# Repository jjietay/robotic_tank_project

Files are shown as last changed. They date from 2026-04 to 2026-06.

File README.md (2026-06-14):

# Autonomous Robotic Tank

<p align="center">
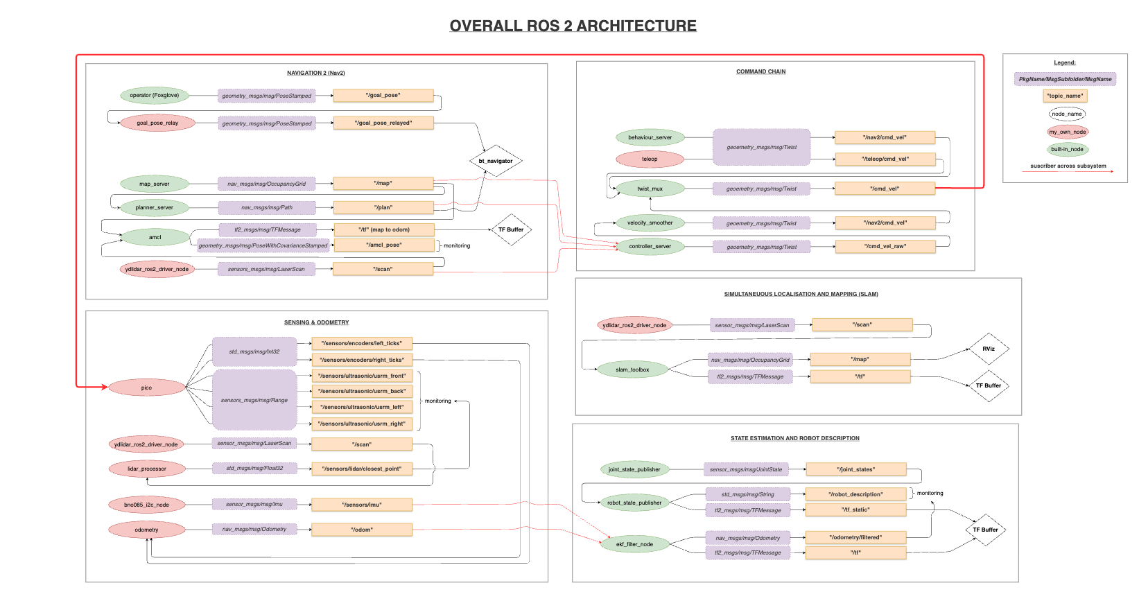
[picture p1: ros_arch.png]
Overall ROS 2 architecture
  
</p>

<p align="center">
  <a href="https://jjietay.github.io/robotic_tank_project/index.html">
    <strong>Read my full documentation & project journey!</strong>
  </a>
</p>

Hi there! Here's a look into my Autonomous Robotic Tank Project. Visit my website in the link above to see my reflection at every stage of this project.

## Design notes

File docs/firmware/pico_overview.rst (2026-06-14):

Pico Overview
=============

See also: :doc:`main.cpp <main_cpp>`

Purpose
-------

Pico W takes care of the hardware.

The Pico W is responsible for:

- Driving the motors through the Cytron motor driver
- Reading the wheel encoders using GPIO interrupts
- Measuring distance with the ultrasonic sensors
- Talking to the ROS 2 system on the Raspberry Pi over micro ROS

Topics
------

The firmware uses these ROS topics:

- ``/cmd_vel`` for the incoming motion command
- ``/sensors/ultrasonic/usrm_front``
- ``/sensors/ultrasonic/usrm_back``
- ``/sensors/ultrasonic/usrm_left``
- ``/sensors/ultrasonic/usrm_right``
- ``/sensors/encoders/left_ticks``
- ``/sensors/encoders/right_ticks``

Layout
------

All of the firmware are in one ``main.cpp`` file + a small set of classes,
motors, encoders, ultrasonic sensors, and PID controller. Shared settings such as pins, robot size, and gains are in ``config.hpp``.

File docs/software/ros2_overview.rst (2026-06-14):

ROS 2 Overview
==============

This page gives a short overview of the ROS 2 software that runs on the
Raspberry Pi 4. The Raspberry Pi handles sensing, state estimation, mapping,
navigation, and the commands that drive the tank. The Pico W handles the low
level motor and sensor work and talks to the Pi over a serial micro ROS link.

The system is made up of a few groups of nodes.

Sensing
    The Pico W publishes wheel encoder ticks and ultrasonic ranges. The lidar
    driver publishes laser scans on ``/scan``. The BNO085 IMU node publishes
    orientation and motion on ``/sensors/imu``.

State estimation
    The odometry node turns encoder ticks into a pose estimate on ``/odom``.
    The EKF from robot_localization fuses ``/odom`` and ``/sensors/imu`` into a
    smoother estimate and broadcasts the ``odom`` to ``base_link`` transform.

Mapping and navigation
    SLAM Toolbox builds a map from the laser scans. Nav2 plans a path to a goal
    and follows it, sending velocity commands for the tank to follow.

Commands
    More than one source can ask the tank to move. Teleop sends keyboard
    commands and Nav2 sends its own commands. The twist_mux node picks one
    based on priority and forwards it as ``/cmd_vel``, which the Pico W reads.

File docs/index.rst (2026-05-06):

Documentation
========================

This documentation covers the full robotic tank project:
My learning process, ROS 2 software on the Raspberry Pi, firmware on the Pico W,
and hardware design and calibration.

.. toctree::
    :maxdepth: 2
    :caption: Sections:

    learning/index
    software/index
    firmware/index

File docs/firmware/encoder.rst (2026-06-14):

Encoder
=======

See also: :doc:`main.cpp <main_cpp>`

Purpose
-------

The ``Encoder`` class reads how far each wheel has turned. It counts the pulses
from a quadrature encoder using GPIO interrupts, and it can report both the tick
count and the wheel speed in metres per second.

How quadrature works
--------------------

A quadrature encoder gives two square wave signals, channel A and channel B,
that are a quarter cycle apart. As the shaft turns, each channel produces rising
and falling edges. The order of the edges on A and B tells you which way the
wheel is turning.

.. list-table::
    :header-rows: 1
    :widths: 30 30 40

    *   - Event
        - Condition
        - Result
    *   - Pin A rises
        - B is LOW (A is not equal to B)
        - ``count++`` (forward)
    *   - Pin A rises
        - B is HIGH (A equals B)
        - ``count--`` (backward)
    *   - Pin B rises
        - A is HIGH (A equals B)
        - ``count++`` (forward)
    *   - Pin B rises
        - A is LOW (A is not equal to B)
        - ``count--`` (backward)

The ``count`` variable is marked ``volatile`` because it is changed inside the
interrupt handler and read in the main loop. That tells the compiler to always
read it back from memory instead of keeping a stale copy in a register.

Scenario 1: A leads B (forward)
-------------------------------

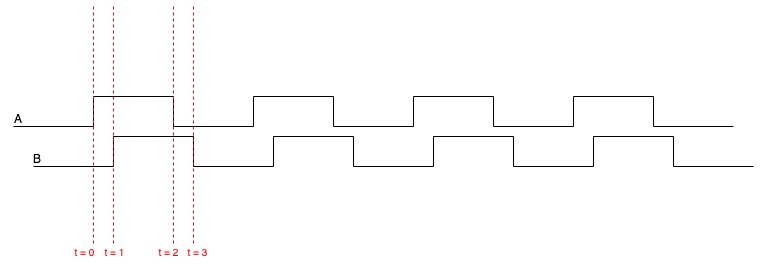
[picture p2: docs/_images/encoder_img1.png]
A leading B


- At t=0, A rises while B is still LOW, so ``count++``
- At t=1, B rises while A is HIGH, so ``count++``
- The result is two counts forward

Scenario 2: B leads A (backward)
--------------------------------

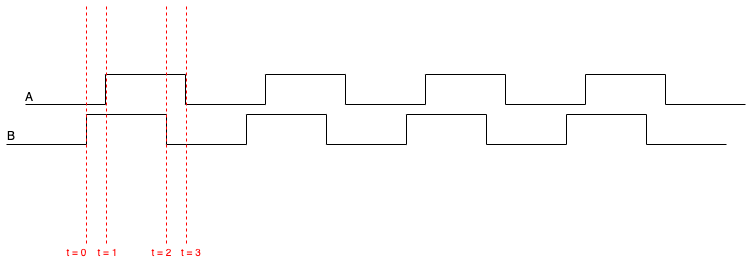
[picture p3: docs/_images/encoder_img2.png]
B leading A


- At t=0, B rises while A is still LOW, so ``count--``
- At t=1, A rises while B is HIGH, so ``count--``
- The result is two counts backward

.. note::

    The count tracks net movement, not total distance. If the tank rolls
    forward one metre and then back one metre, the count returns to zero.

Counts per wheel turn
---------------------

The number of counts for one full turn of the wheel depends on the encoder
pulses, the gearbox, and the fact that the decoder counts both edges of both
channels:

.. math::

    \text{counts per wheel turn} = 4 \times \text{PPR} \times \text{gear reduction}

For this tank the encoder has 11 pulses per motor turn and the gearbox reduction
is 131, so:

.. math::

    4 \times 11 \times 131 = 5764 \text{ counts per wheel turn}

Setup
-----

The constructor works out the wheel circumference from the diameter, works out
the counts per wheel turn, and sets up the pins. Both channel pins are inputs
with pull up resistors, which hold them HIGH when there is no signal and stop
false edges from electrical noise.

The Pico allows only one GPIO interrupt callback per core. So the first encoder
registers the shared callback, and any later encoder only enables its pins and
reuses that same callback:

.. code-block:: cpp

    gpio_set_irq_enabled_with_callback(pin_a, GPIO_IRQ_EDGE_RISE | GPIO_IRQ_EDGE_FALL,
                                       true, &Encoder::irq_handler);

    gpio_set_irq_enabled(pin_a, GPIO_IRQ_EDGE_RISE | GPIO_IRQ_EDGE_FALL, true);
    gpio_set_irq_enabled(pin_b, GPIO_IRQ_EDGE_RISE | GPIO_IRQ_EDGE_FALL, true);

Handling the interrupt
----------------------

Every edge goes to the one static ``irq_handler``, which loops over the
registered encoders and calls ``handle_irq`` on each. ``handle_irq`` first
checks that the pin belongs to that encoder, then applies the quadrature rule
to move the count up or down.

Methods
-------

.. cpp:function:: int get_count()

Returns the signed tick count. Interrupts are turned off for the moment of the
read so the value cannot change halfway through. If the encoder was set up as
inverted, the sign is flipped.

.. cpp:function:: float get_vel()

Returns the wheel speed in metres per second. It works out the time since the
last call, finds the change in counts, turns that into a distance, and divides
by the time:

.. math::

    v = \frac{\Delta\text{counts}}{\text{counts per wheel turn}} \times
        \frac{C}{\Delta t}

where ``C`` is the wheel circumference. The time step is floored at one
millisecond to keep the result steady, the first call returns zero, and the
speed is passed through an exponential moving average so it is smoother.

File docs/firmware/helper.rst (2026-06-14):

Helper Functions
================

See also: :doc:`main.cpp <main_cpp>`

Purpose
-------

These are the small helper functions in ``main.cpp``.

clampf
------

.. code-block:: cpp

   static inline float clampf(float x, float lo, float hi)
   {
       if (x < lo) return lo;
       if (x > hi) return hi;
       return x;
   }

Keeps a value inside a low and high limit. The control loop uses it to keep the
motor duty inside the range from -1 to 1 after the feedforward and
PID are added together.

init_range_msg
--------------

.. code-block:: cpp

   static void init_range_msg(sensor_msgs__msg__Range* msg, uint8_t rad_type,
                              float fov, float min_r, float max_r)
   {
       msg->radiation_type = rad_type;
       msg->field_of_view  = fov;
       msg->min_range = min_r;
       msg->max_range = max_r;
       msg->range  = 0.0f;
   }

Fills in the fixed fields of a range message: the type, the cone angle, and the
smallest and largest distance the sensor can report. The four ultrasonic
messages are set up with the same call, so they all share the same settings and
only differ in their frame name and their measured value.

set_msg_stamp
-------------

.. code-block:: cpp

   static void set_msg_stamp(std_msgs__msg__Header* header)
   {
       uint64_t now_us = time_us_64();
       header->stamp.sec = now_us / 1000000ULL;
       header->stamp.nanosec = (now_us % 1000000ULL) * 1000ULL;
   }

Stamps a message with the current time from the Pico clock, split into seconds
and nanoseconds the way ROS 2 expects. Every published message uses this same
clock, which keeps the timestamps consistent for the Raspberry Pi to use.

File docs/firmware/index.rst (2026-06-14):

Firmware
========

This section covers the firmware that runs on the Pico W. The Pico W drives the motors, reads the wheel
encoders, fires the ultrasonic sensors, and communicates to the Raspberry Pi over a
serial micro ROS link.

Overview
--------

.. toctree::
    :maxdepth: 2

    pico_overview

Code
----

.. toctree::
    :maxdepth: 2

    main_cpp

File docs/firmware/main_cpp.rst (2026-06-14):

main.cpp
========

See also: :doc:`Pico Overview <pico_overview>`

Purpose
-------

``main.cpp`` sets up the hardware, sets up the
micro ROS link, and then runs the control loop that keeps the tank moving.

What it does
------------

- Sets up GPIO, PWM, timing, and interrupts
- Builds the four ultrasonic sensors, the motor driver, the two encoders, and
  the two PID controllers
- Sets up the micro ROS node, the ``/cmd_vel`` subscriber, and the publishers
- Reads ``/cmd_vel`` and turns it into a target speed for each track
- Publishes ultrasonic ranges and encoder ticks back to ROS 2
- Runs the control loop at 100 Hz

Structure
---------

The file is split into a few parts:

- The :doc:`Electronics <main_cpp>` base class gives every hardware class a name
  and a status
- :doc:`Ultrasonic <ultrasonic>` measures distance with a timeout
- :doc:`Motor <motor>` drives the Cytron motor driver
- :doc:`Encoder <encoder>` counts wheel ticks using interrupts and works out
  wheel speed
- :doc:`PID <pid>` corrects the wheel speed
- :doc:`micro ROS <microros>` holds the subscriber, the publishers, and the
  command callback
- :doc:`Helper functions <helper>` set up range messages, stamp messages, and
  clamp values
- :doc:`main() Loop <main_loop>` runs the repeating control cycle

Related components
------------------

.. toctree::
    :maxdepth: 1

    encoder
    ultrasonic
    motor
    pid
    helper
    microros
    main_loop

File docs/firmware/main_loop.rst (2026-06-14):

main() Loop
===========

See also: :doc:`main.cpp <main_cpp>`

Startup
-------

Before the loop starts, ``main()`` does a one time setup:

1. Starts USB and serial output, then waits two seconds so the host can attach.
2. Builds the four ultrasonic sensors, the motor driver, the two encoders, and
   the two PID controllers.
3. Sets up the micro ROS transport over the Pico UART and creates a node named
   ``pico``.
4. Creates the ``/cmd_vel`` subscriber and the publishers for the ultrasonic
   ranges and the encoder ticks.
5. Fills in the range message settings and the frame names.
6. Adds the ``/cmd_vel`` subscription to the executor.

The publishers and subscriber are:

.. list-table::
   :header-rows: 1
   :widths: 30 35 35

   * - Role
     - Topic
     - Message type
   * - Subscriber
     - ``/cmd_vel``
     - ``geometry_msgs/msg/Twist``
   * - Ultrasonic publishers (4x)
     - ``/sensors/ultrasonic/usrm_*``
     - ``sensor_msgs/msg/Range``
   * - Encoder publishers (2x)
     - ``/sensors/encoders/*_ticks``
     - ``std_msgs/msg/Int32``

The control loop
----------------

After setup, ``main()`` runs forever at about 100 Hz. Each pass through the
loop does the following.

1. Mark the time
~~~~~~~~~~~~~~~~

The loop records the start time so it can pace itself to 100 Hz at the end.

2. Handle ROS messages
~~~~~~~~~~~~~~~~~~~~~~~

.. code-block:: cpp

   rclc_executor_spin_some(&executor, RCL_MS_TO_NS(2));

This gives the executor a short period of time to read new micro ROS messages.
When a new ``/cmd_vel`` arrives, the callback updates the left and right target
speeds in metres per second.

3. Fire one ultrasonic sensor
~~~~~~~~~~~~~~~~~~~~~~~~~~~~~

Only one ultrasonic sensor fires per cycle, and only on every third cycle. A
rotating index picks the front, back, right, or left sensor in turn. The chosen
sensor takes a reading, the range and timestamp are filled in, and the message
is published. Spacing the sensors out keeps a slow reading from blocking the
loop timing.

4. Read the command and check the watchdog
~~~~~~~~~~~~~~~~~~~~~~~~~~~~~~~~~~~~~~~~~~~

The loop copies the latest target speeds. If no ``/cmd_vel`` has arrived for
more than 500 ms, both targets are set to zero, so the tank stops if the link
goes quiet.

5. Safety stop
~~~~~~~~~~~~~~

The loop looks at the average target speed to decide if the tank wants to go
forward or backward. If it wants to go forward and the front sensor sees an
object closer than the front stop distance, both speeds are set to zero. The
same check is done for the back sensor when reversing.

6. Feedforward and PID
~~~~~~~~~~~~~~~~~~~~~~~

The loop reads the measured speed of each wheel from the encoders. For each
side it works out a feedforward duty from the target speed, then adds the PID
correction, and clamps the result to the range from negative one to one:

.. code-block:: cpp

   float ff_l = clampf(vel_l / V_MAX_MPS, -1.0f, 1.0f);
   duty_l = clampf(ff_l + pid_l.calculate(vel_l, meas_l), -1.0f, 1.0f);

When both targets are zero, the PID controllers are reset and the duty is set
to zero, so the integral term does not build up while the tank is stopped.

7. Drive the motors
~~~~~~~~~~~~~~~~~~~

.. code-block:: cpp

   MOTOR.move(duty_l, duty_r);

The motor class takes the two duty values and sets the direction pins and PWM
levels.

8. Publish encoder ticks
~~~~~~~~~~~~~~~~~~~~~~~~

The loop reads the signed tick count from each encoder and publishes them so
the odometry node on the Raspberry Pi can use them.

9. Pace the loop
~~~~~~~~~~~~~~~~

The loop busy waits until 10 ms have passed since the start time, which gives a
steady 100 Hz rate.

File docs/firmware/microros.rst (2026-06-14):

micro ROS
=========

See also: :doc:`main.cpp <main_cpp>`

Purpose
-------

This page covers the micro ROS parts of the firmware. micro ROS is the bridge
between the ROS 2 system on the Raspberry Pi 4 and the control loop on the
Pico W.

What it sets up
---------------

The firmware creates:

- one ``/cmd_vel`` subscriber (``geometry_msgs/msg/Twist``),
- four ultrasonic range publishers (``sensor_msgs/msg/Range``),
- two encoder tick publishers (``std_msgs/msg/Int32``),
- the message buffers for each of these,
- the micro ROS support objects: the allocator, the support struct, the
  executor, and the node

Node and transport
------------------

Micro ROS uses the Pico UART as its transport, then
creates a node that shows up in the ROS 2 graph on the Raspberry Pi:

.. code-block:: cpp

   rmw_uros_set_custom_transport(
       true, NULL,
       pico_serial_transport_open,  pico_serial_transport_close,
       pico_serial_transport_write, pico_serial_transport_read);

   allocator = rcl_get_default_allocator();
   rclc_support_init(&support, 0, NULL, &allocator);
   rclc_node_init_default(&node, "pico", "", &support);

The node is named ``pico``, so tools like ``ros2 node list`` on the Pi can find
it.

The command callback
--------------------

When a ``/cmd_vel`` message arrives, the callback reads the forward speed and
the turn rate and splits them into a target speed for each track:

.. code-block:: cpp

   void cmd_vel_callback(const void* msg_in) {
       const auto* msg = (const geometry_msgs__msg__Twist*)msg_in;
       float v_mps = (float)msg->linear.x;
       float w_rps = (float)msg->angular.z;
       target_vel_l_mps = v_mps - w_rps * (WHEEL_BASE_M * 0.5f);
       target_vel_r_mps = v_mps + w_rps * (WHEEL_BASE_M * 0.5f);
       last_cmd_vel_time_us = time_us_64();
   }

This is the standard differential drive split. The forward speed moves both
tracks together, and the turn rate speeds up one track and slows the other.
Both targets are kept in metres per second, which is what the control loop and
the encoders use. The time of the last command is saved so the loop can stop
the tank if commands stop arriving.

The executor
------------

The executor checks the transport for new messages and runs the callback:

.. code-block:: cpp

   rclc_executor_init(&executor, &support.context, 1, &allocator);
   rclc_executor_add_subscription(
       &executor, &cmd_vel_sub, &cmd_vel_msg, &cmd_vel_callback, ON_NEW_DATA);

The control loop calls ``rclc_executor_spin_some`` once per cycle, so the
callback runs often without blocking the rest of the loop.

Data flow
---------

End to end, the flow is:

1. A node on the Raspberry Pi publishes ``/cmd_vel``.
2. micro ROS on the Pico reads it and updates the two target speeds.
3. The control loop reads the sensors, runs the safety checks and the PID, and
   drives the motors.
4. The ultrasonic ranges and encoder ticks are published back to ROS 2.

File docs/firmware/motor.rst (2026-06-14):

Motor
=====

See also: :doc:`main.cpp <main_cpp>`

Purpose
-------

The ``Motor`` class drives the two tracks through the Cytron MDD10A motor
driver. One ``Motor`` object controls both the left and the right side.

How it works
------------

For each side the driver has two pins:

- a direction pin that sets forward or reverse
- a PWM pin that sets the speed

In this design ``l_dir_pin`` and ``l_pwm_pin`` control the left side, and
``r_dir_pin`` and ``r_pwm_pin`` control the right side.

The move method
---------------

``move(duty_left, duty_right)`` takes a duty value for each side in the range
from negative one to one:

- ``+1`` is full speed forward,
- ``0`` is stop,
- ``-1`` is full speed reverse

Before the command reaches the pins, ``move`` does three things:

1. **Trim**

   Each side is scaled by its trim factor. This helps account for manufacturing defects for straight driving.

2. **Minimum duty**

   A small duty often will not move the motor at all. If the
   original command was above the minimum, the duty is pushed up to at least the
   minimum so the wheel actually turns. The minimum is only applied when the
   original command was accepted, so it does not cancel out the trim.

3. **Invert**

   If a side is wired in reverse, an invert flag flips its sign, so
   the rest of the code can always treat positive as forward.

Setting one side
----------------

Each side is then sent to the driver:

.. code-block:: cpp

   void Motor::set_one_side(uint dir_pin, uint pwm_pin, float duty)
   {
       if (duty >  1.0f) duty =  1.0f;
       if (duty < -1.0f) duty = -1.0f;
       gpio_put(dir_pin, duty >= 0.0f ? 1 : 0);
       pwm_set_gpio_level(pwm_pin, (uint16_t)(std::fabs(duty) * (float)PWM_TOP));
   }

The duty is clamped to the safe range, the sign sets the direction pin, and the
size sets the PWM level. ``PWM_TOP`` is the full scale value, so a duty of one
gives the highest PWM level.

Other methods
-------------

.. cpp:function:: void stop()

Sets both sides to zero so both motors stop.

Setup
-----

The constructor stores the pins, the invert flags, and the trim values, sets the
two direction pins as outputs, and sets up PWM on the two speed pins.

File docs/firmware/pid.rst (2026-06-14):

PID
===

See also: :doc:`main.cpp <main_cpp>`

Purpose
-------

The ``PID`` class corrects the wheel speed. Each wheel has its own controller.
It compares the speed you asked for with the speed the encoder measured, and it
returns a duty correction that nudges the wheel towards the target.

Units
-----

- The setpoint and the measured value are both in metres per second
- The output is a duty value in the range from negative one to one, the same
  range the motor class uses

What calculate does
-------------------

``calculate(setpoint, measured)`` runs one step of the controller:

1. **Time step**

   It calculates the time since the last call. If that time looks
   wrong, for example zero or too large after a pause, it falls back to ten
   milliseconds.

2. **Error**

   The error is the setpoint minus the measured speed.

3. **Proportional**

   The P term is the gain times the error.

4. **Integral**

   The error times the time step is added to a running total. The
   total is held inside a fixed limit so it cannot grow without bound. The I
   term is the gain times that total.

5. **Derivative**

   The D term is the gain times the change in error over the
   time step. It is skipped on the very first call so a sudden jump does not
   cause a kick.

6. **Sum and limit**

   The three terms are added. If the sum goes past the output
   limit, the output is held at the limit and the integral is wound back by the
   amount it went over. That keeps the integral from building up while the
   output is maxed out.

Resetting
---------

``reset()`` clears the integral, clears the last error, and marks the next call
as the first one. The control loop calls this whenever the tank is told to stop,
so the controller starts clean the next time the tank moves.

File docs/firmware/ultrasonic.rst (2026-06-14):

Ultrasonic Sensor
=================

See also: :doc:`main.cpp <main_cpp>`

Purpose
-------

The ``Ultrasonic`` class drives one ultrasonic distance sensor. Each sensor has
a trigger pin and an echo pin. The class fires a reading on demand and returns
the distance in metres.

How the sensor works
--------------------

The sensor has a transmitter and a receiver. It sends out a short burst of sound
above the range of human hearing, then listens for the echo that bounces back
off an object. The time the echo takes to return tells you the distance.

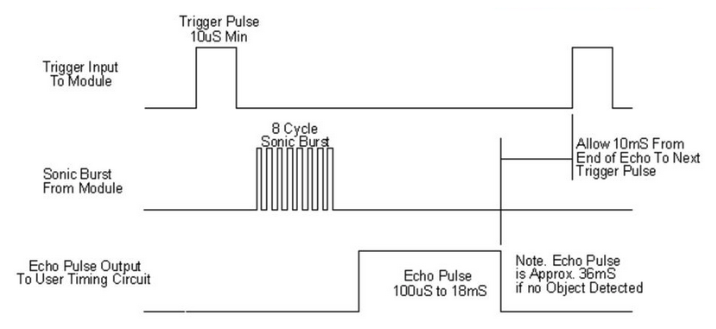
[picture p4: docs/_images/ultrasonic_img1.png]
Ultrasonic timing


A reading has four parts:

1. The trigger pin is pulled HIGH for a short pulse, then LOW. This tells the
   sensor to fire.
2. The sensor sends out the burst of sound.
3. The echo pin goes HIGH while the sensor waits for the sound to come back.
4. When the echo returns, the echo pin goes LOW. The time the echo pin stayed
   HIGH is the round trip time of the sound.

Working out the distance
------------------------

Once the echo time is known, the distance is:

.. math::

    d = \frac{t \times v_s}{2}

where ``t`` is the echo time in seconds and ``v_s`` is the speed of sound, about
346 metres per second at room temperature. The result is halved because the
sound travels to the object and back, so the echo time covers twice the
distance. In this code the result is returned in metres.

The update method
-----------------

``update()`` fires the sensor and waits for the echo. It is a blocking call, so
it holds the processor until the echo returns or a timeout is reached. The
timeout is about 38 milliseconds. The return values are:

- ``-1.0`` when the echo never starts, which means no object or a wiring fault
- ``-2.0`` when the echo starts but never ends, which can happen when an object
  is far too close
- any positive value, which is a valid distance in metres

Firing one at a time
--------------------

In the main loop only one sensor fires per cycle, using a rotating index. Since
each reading can block for a while, spacing them out keeps the loop timing
steady and stops one sensor from hearing another sensor burst.

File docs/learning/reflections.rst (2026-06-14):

Reflections
================================

See also: :doc:`ROS 2 Notes <ros2>`

.. note::
   This is a long reflection, if you wanna just skip to major periods just before the final results, click one of these dates in the right corner table of dates:

   - 30 May 2026 --> RViz2 
   - 7 June 2026 --> Nav2

A personal log of difficulties faced, solutions found, and lessons learned
while building the autonomous tank.

Background
----------
From the two years into uni, I realised I wasn't actually learning the things I was interested in which are AI and robotics. I have always wondered how do robots "think". After learning about neural networks and transformers, I realise I wanted to build a robot. Also, uni didn't teach me any of these. Moreover, I needed to take matters in my own hands and actually learn this such that it will help me in expanding my knowledge pool and also in my future career. 

I figured if I could build something real using sensors, SLAM, Nav2, and actually have a working autonomous robot that I fully understand how its done, then I'd come out the other side actually understanding robotics. Moreover, with my VLA-based FYP for robotics systems in my final year, having this hands-on foundation felt important to me.

I decided to build a self-driving tank. Why a tank you may ask. If I'm being honest, part of it is that I've been fascinated by tanks since I was a kid (spent abit too much time playing world of tanks), so building one felt like the obvious choice. But beyond the nerdy appeal, I also knew that actually building something physical was the only way I'd retain any of this. I needed something I could break, fix, and learn from.

----

26 Feb 26 - Start of Project
------------------------------

After researching and consulting AI what I should purchase, I spend nearly a crazy ~$200 out of my own pocket to purchase the items that included Rasberry Pi 4, Pico W, Pi Camera Module 2, YDLidar X3 Pro, basic arduino car kit (included with motors), H bridge, 18560 batteries.

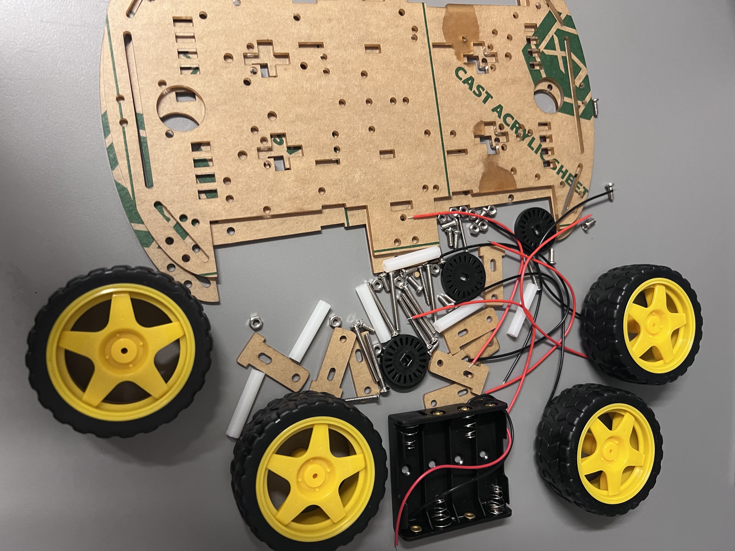
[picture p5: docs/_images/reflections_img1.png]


   Figure 1: Before building version 1

When the kit in Figure 1 came, I couldn't wait to start. I followed some YouTube Tutorial on it and started building. I learnt how to write a simple micropython script and then make it such that it recieves the velocity commands over USB to my RPI4. I've heard that ROS was a pain to set up, so I deliberately kept it out of the picture, so I can focus in ensuring hardware and my python script is correct.

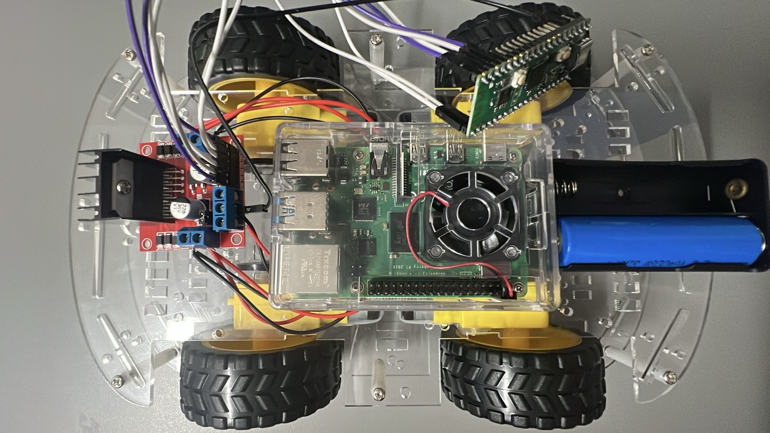
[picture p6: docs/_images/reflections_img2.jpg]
After building


   Figure 2: After building version 1

As shown in Figure 2 above, my current build contains RPI4, Pico W, 18650 batteries, the L298N H Bridge that is wired to my motors. The L298N required many connections. For a 4 wheel (4 motor) setup, I had to combine the motor voltage wires together for each side. Dir pins control both motors at each side.

This "simple" setup, took me awhile because of many problems. The table below shows some problems faced and respective solutions.

.. list-table::
   :header-rows: 1
   :widths: 50 50

   *  - Problem
      - Solution

   *  - weak (loose) connection
      - wiggle the wires to make sure they don't just fall out and secure them if they do fall out
   *  - code issues
      - make changes to the code and verify with AI (my project mentor)
   *  - motor forward/backward direction issues
      - switch the pins (best to switch it hardware wise than software which might confuse myself in the future when reviewing the codebase)
   *  - cold solder joints
      - fill edges of soldering iron's tip with solder first, repeat it multiple times, and ensure that soldering joint is hot

This first success building the car made me more motivated and excited to continue on with my project. 

.. raw:: html

   <figure style="text-align: center;">
   <video width="640" height="360" controls style="display: block; margin: auto;">
      <source src="../_static/reflections_vid1.mp4" type="video/mp4">
      Your browser does not support the video tag.
   </video>
   <figcaption style="color: gray; margin-top: 0.8em;">Video 1: Car moving around and spinning</figcaption>
   </figure>

Video 1 above shows my car finally moving, controlled via my keyboard, WASD.

----

12 Mar 26 - 1st Real Difficulty
--------------------------------

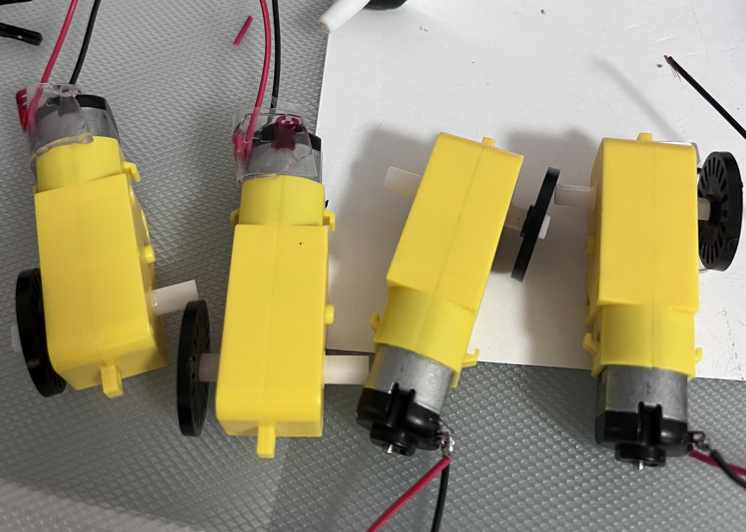
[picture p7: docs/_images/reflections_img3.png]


   Figure 3: Poor solder joint on my motors

From Figure 3, we can see that I took out the motors. This is because the motors were not reliable due to bad solder joint.

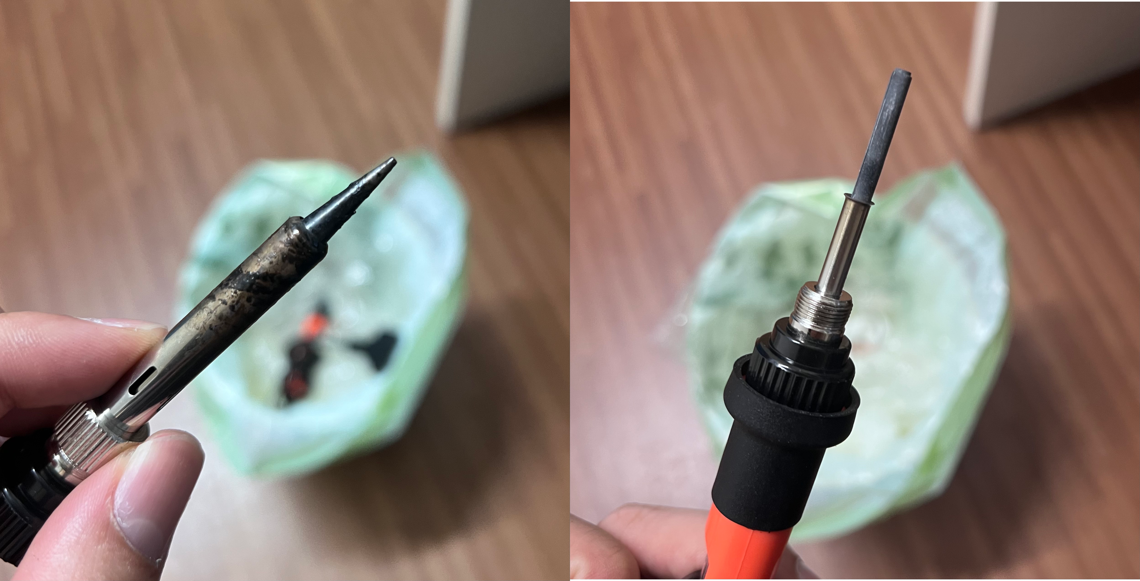
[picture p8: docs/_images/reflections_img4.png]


   Figure 4: Poor soldering iron quality

From Figure 4, you can tell that I was using a really cheap soldering iron and the solder connections became so unreliable, sometimes the car won't even move. This was when I knew I had to invest in a good soldering setup to ensure issues like these won't arise in the future again. I bought a new soldering iron (reddit users recommendations) and seperate quality solder with higher flux percentage.

When the new soldering iron came, I soldered on new pair of wires onto the motor flaps and everything worked. I knew the next steps were to add my LIDAR and bigger portable onto my car.

26 Mar 26 - Improved Chassis, or is it?
-----------------------------------------

When I fitted the my bigger powerbank, everything changed. The whole system got heavier, and my cheap TT motors were struggling to move the car. When moving forward or backwards, it worked fine. But when it was tank turning left or right, it didn't budge. This is because the TT motors are not producing enough torque force to overcome the static friction.

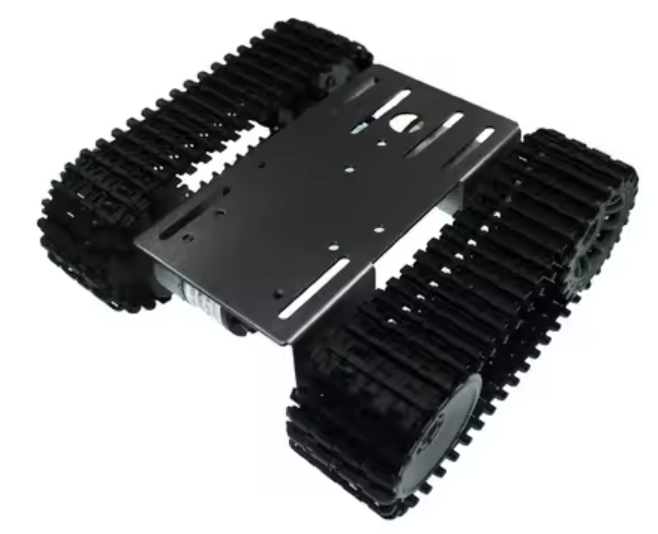
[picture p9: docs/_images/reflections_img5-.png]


   Figure 5: New chassis & motor

From Figure 5, we can see that I am using the TP-101 chassis with 2 provided 33GB-520 motors. The tank chassis certainly helped with distribution the weight across the tracks.

The specifications of both are displayed in the table below.

.. list-table::
   :header-rows: 1
   :stub-columns: 1
   :widths: 15 20 20

   *  -
      - Old Chassis w TT Motors
      - New Chassis w 33GB-520 Motors

   *  - Number of Motors
      - 4 Motors
      - 2 Motors

   *  - Voltage
      - 3-6 V
      - 6-12 V

   *  - No-load Speed
      - 90-200 RPM
      - 170-350 RPM

   *  - Max Torque (all motors combined)
      - 3.2 kg cm
      - 5 kg cm

   *  - Gearbox
      - Plastic
      - All metal

   *  - Current (no-load)
      - 170-250 mA
      - 100 mA

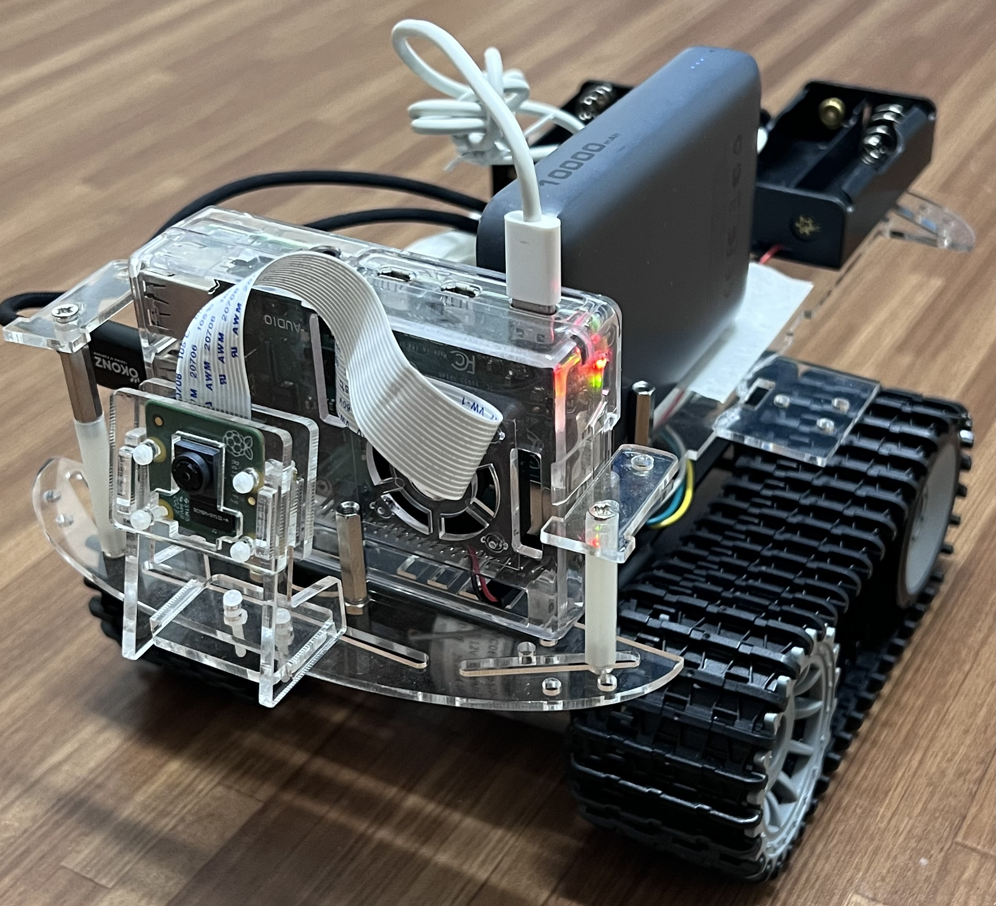
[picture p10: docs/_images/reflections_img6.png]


   Figure 6: After building

Figure 6 shows the final product after building. Notice the rasberry camera module 2 installed. I tested it by streaming live feed and viewing it on my macbook via VLC player. I noticed that the camera FOV is small. This might impact the robot's ability to see things at corners of the image. Therefore, I have decided to get another camera that have a greater FOV.

9 Apr 26 - Camera problems
---------------------------

.. list-table::
   :header-rows: 1
   :stub-columns: 1
   :widths: 15 20 20

   *  -
      - RPI Camera Module 2
      - OV5647 130 degrees

   *  - Sensor
      - Sony IMX219
      - OmniVision OV5647

   *  - Resolution
      - 8MP
      - 5MP

   *  - Horizontal FOV
      - 62.2 degrees
      - 130 degrees

   *  - Focal Length
      - F2.0
      - F2.9

When I got the OV5647, I tried it and observed a larger FOV. However, when it took it and pulled the latch on the Camera Serial Interface (CSI) to unlock it (so that I can remove the ribbon attached to my OV5637, it **broke**.

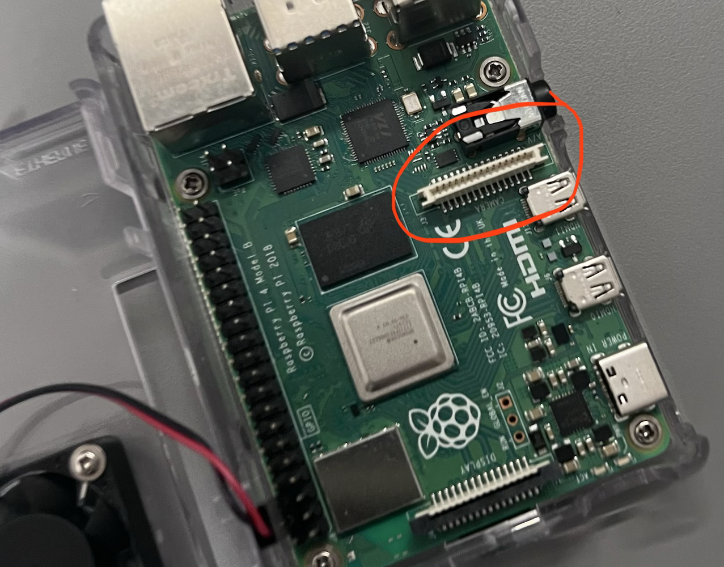
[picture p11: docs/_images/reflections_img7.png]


   Figure 7: Broken latch

Figure 7 shows my destroyed CSI. I looked up online and realised that the CSI is notorious for getting damaged. I could replace the whole CSI piece and solder on a new one, or I could get a USB camera. I didn't take the risk, and bought a USB camera with similar FOV. 

9 Apr 26 - Lack of Encoder & Motor Driver Upgrade
---------------------------------------------------

I began researching more into SLAM, and realised that I need an encoder for my wheel so that I can calculate the odometry for my base_link.

I had a choice of adding an encoder to my current motor, but it wasn't feasible as it might increase inaccuracies (since there are more hardware building), and I wouldn't wanna mess up the encoder accuracy since that directly affects drift.

Therefore, I decided to purchase the JBG37-520-12V-60RPM with Encoder already attached to it. The table below shows the differences.

.. list-table::
   :header-rows: 1
   :stub-columns: 1
   :widths: 15 20 25

   *  - 
      - 33GB-520
      - JBG37-520-12V-60RPM with Encoder

   *  - Encoder
      - No
      - Yes

   *  - Working Voltage
      - 6-12 V
      - 12 V

   *  - Rated Torque (per motor)
      - 1.6 kg cm
      - up to 30 kg cm (at 37 RPM)

   *  - No-load Speed
      - 170-350 RPM
      - 70 RPM

From the table above, we can see that JBG37-520-12V-60RPM motor gives ALOT of torque, and that is good for my application where speed is not really important, but torque and precision in movement is.

JBG37-520 uses AB-phase Quadrature Hall Encoders. The encoder outputs 11 Pulses per Revolution (PPR). This means that the effective output shaft resolution is ``11 * gear_ratio``. For this 60RPM variant, it is around 1848 counts/rev which is excellent resolution.

Additionally, the existing H-bridge proved to be quite inefficient, dissipating a significant amount of energy as heat, with a voltage drop of nearly 2V across it. To address this, I sourced the Cytron MDD10A Dual Channel 10A DC Motor Driver, which uses a fully NMOS H-Bridge design to achieve significantly lower voltage drop and improved efficiency.

16 Apr 26 - Motor Mismatch + LIDAR's custom fit
-------------------------------------------------

When the motor came, I eagerly tried to yoink it in place. But to my surprise, it didn't fit. I did check the shaft dimensions before purchasing, but turned out the old motor I was using had a different sizing from the spec sheet found online.

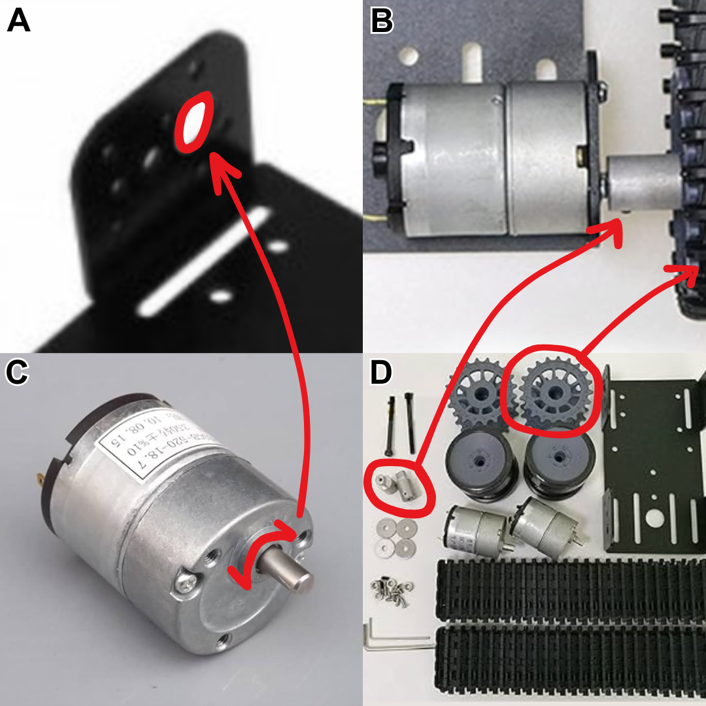
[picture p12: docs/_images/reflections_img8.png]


   Figure 8: Motor to Chassis Connection

From Figure 8 above, we can see the different parts required to connect the motor shaft to the drive wheel. First, the mini motor housing extrusion of C has to fit through the hole in A. Coupler in D is then attached onto motor shaft, and attached to drive wheel as shown in B.

However, my new motor's housing extrusion can't fit through the hole in A, and the coupler couldn't attach to the motor shaft.

To fix this, I have decided to customize my chassis by:

1) **3D printing** my own custom chassis with custom coupler
2) Mounting my LIDAR on custom **acrylic**

27 Apr 26 - Acrylic
-----------------------

For acrlyic, my main goal is just to drill holes so that I can fit my LIDAR. 

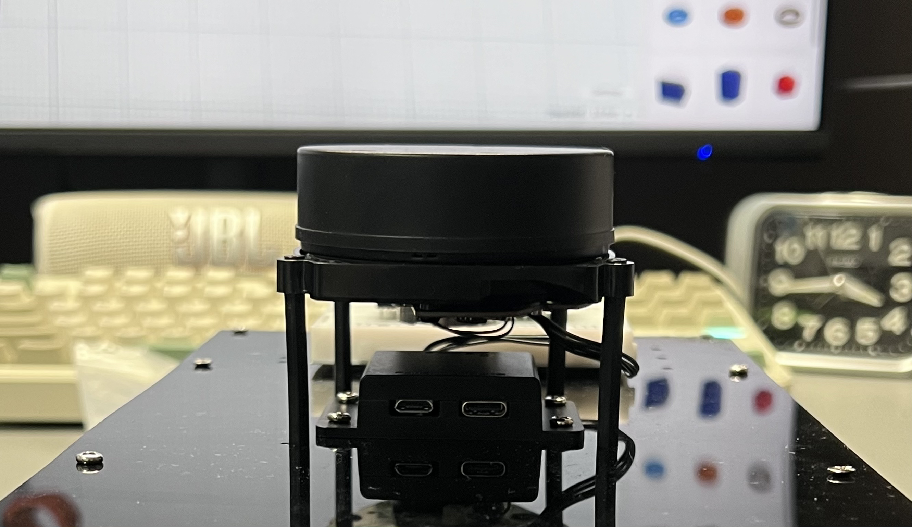
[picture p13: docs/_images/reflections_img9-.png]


   Figure 9: 3D model of chassis

Figure 9 shows how it looked like.

20 Apr 26 - 3D Prints
-----------------------

As for the 3D printing, I saw this as an opportunity for me to learn 3D design, and I downloaded Autodesk Fusion. I spent the first few hours watching youtube tutorials and then I got started.

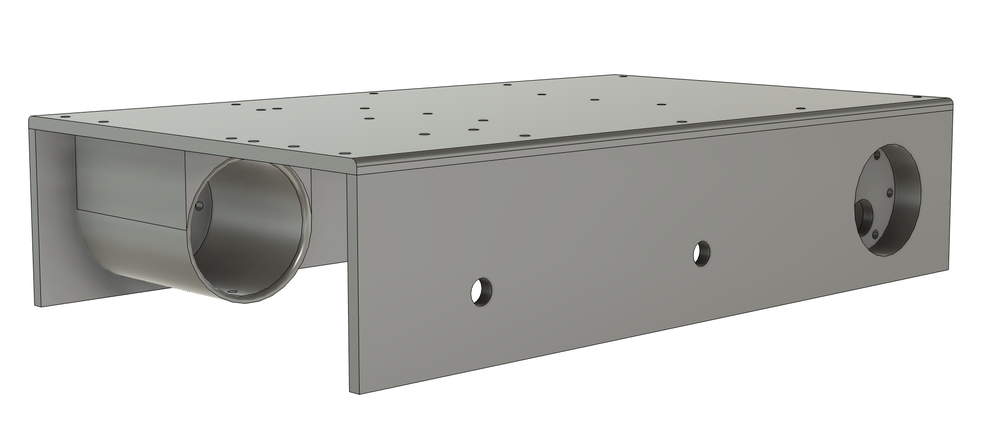
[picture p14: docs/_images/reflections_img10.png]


   Figure 10: 3D model of chassis

Figure 10 shows the overall 3D view of the chassis. It features motor mounts for me to slide in the motors and secure with screws. At the top are holes for me to add standoffs to secure my components such as powerbank, motor driver, RPI4 and 18650 batteries.

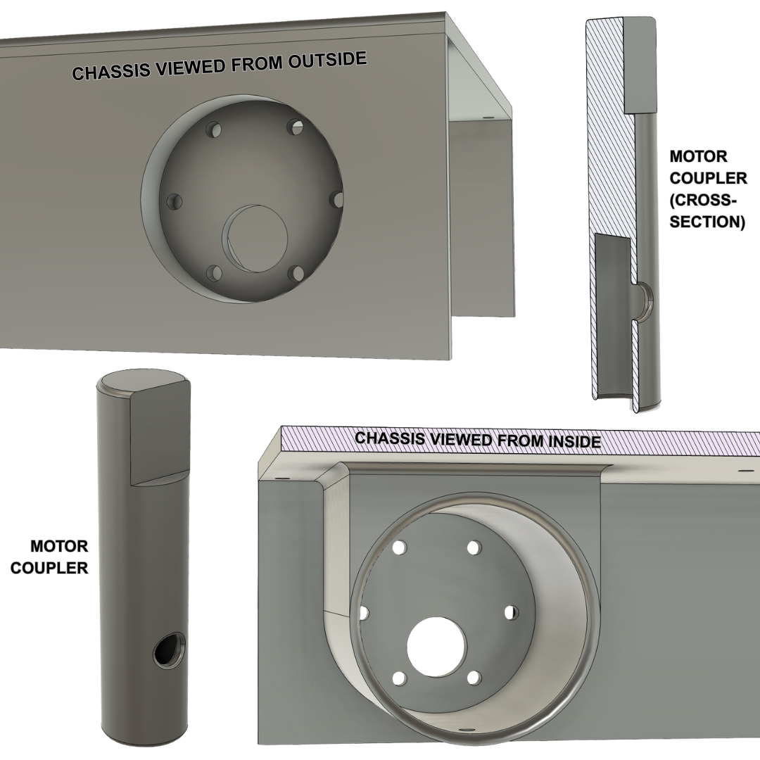
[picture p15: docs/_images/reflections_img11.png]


   Figure 11: Details of Chassis & Motor Coupler

Figure 11 shows the details of the designs. The motor housing is intentionally pushed slightly inwards due to its longer extrusion (at the shaft) compared to the previous motor. Moreover, there are also 5 screw holes for secure fit. As for the coupler, it is a simple design where the shaft slides into the bottom and the drive wheel slides in at the top.

Some issues faced with this design was that the shaft turned while the coupler stayed in place. This made me learn about tolerances and how we have to account for that. Also, the length of coupler was not accurate. This meant that my drive wheel and supporting wheel were not aligned with respect to the track. Therefore, I had to re-measure and print a few more with (slight) differing lengths.

26 Apr 26 - How I learn coding/ROS 2
--------------------------------------
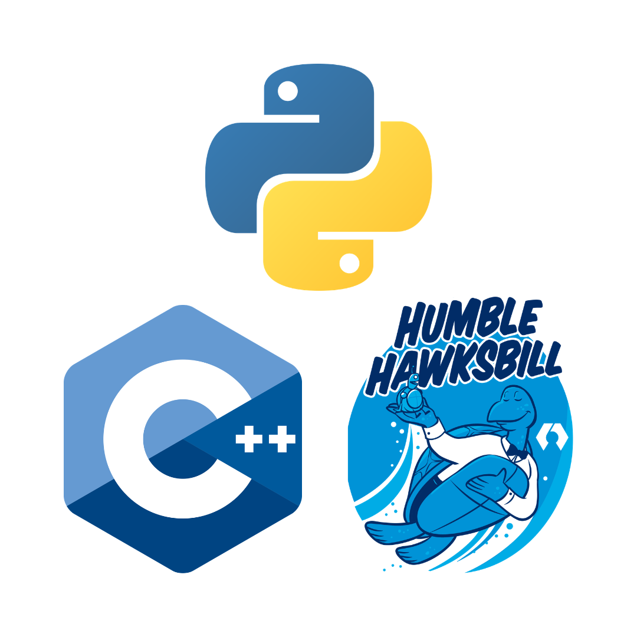
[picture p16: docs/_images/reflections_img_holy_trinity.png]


   ~ holy trinity ~

Throughout the whole process while waiting for shipment to arrive (usually takes a week or two), I would take this time to brush up on my python, learn my C++, and also learn ROS from scratch. I found it a very big challenge at the beginning because this is all completely new to me.

My process was as such. First I used AI to teach me the relevant concepts. I will then ask it to generate some questions/practice for me to do. After that, it will check my code and also my output and give me my score. If I still don't feel confident about that particular exercise, I will ask it generate another one. Only when I understand at least 80% of it, I will ask it to teach me another concept. The exercise portion is so that I can learn actively instead of passively.

Also, I chose python for my codebase for RPI4 because its easier. When the full pipeline works, I might explore C++.

27 Apr 26 - Minor Upgrades: Ultrasonic Sensors and Electrical Schematics
-------------------------------------------------------------------------

I decided to get some new ultrasonic sensors and then decided to plan out the schematics and pin allocations. 

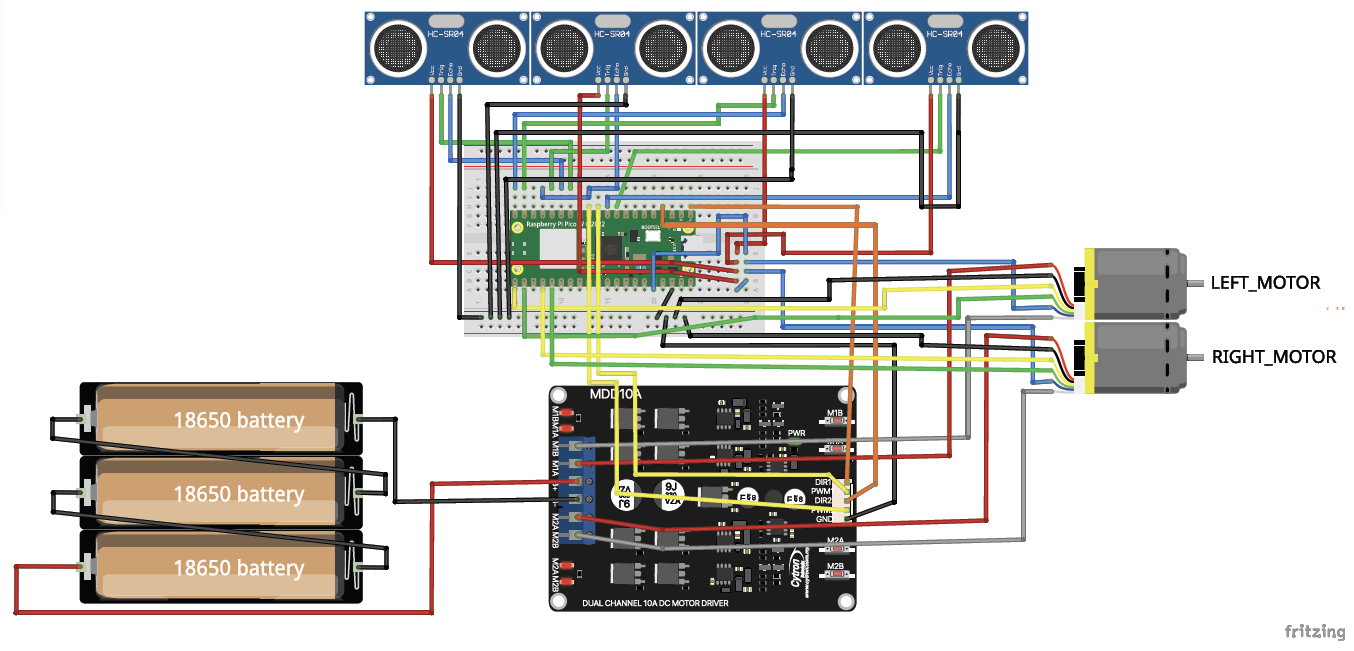
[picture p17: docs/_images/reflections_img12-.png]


   Figure 12: Fritzing Schematics

Figure 12 shows the schematics that I have created using Fritzing (an open-soruce application). It shows my main electronics used for connections. Since this is just prototyping, I am using a half sized breadboard and jumper wires for my wiring.

28 Apr 26 - Finished Hardware
-------------------------------

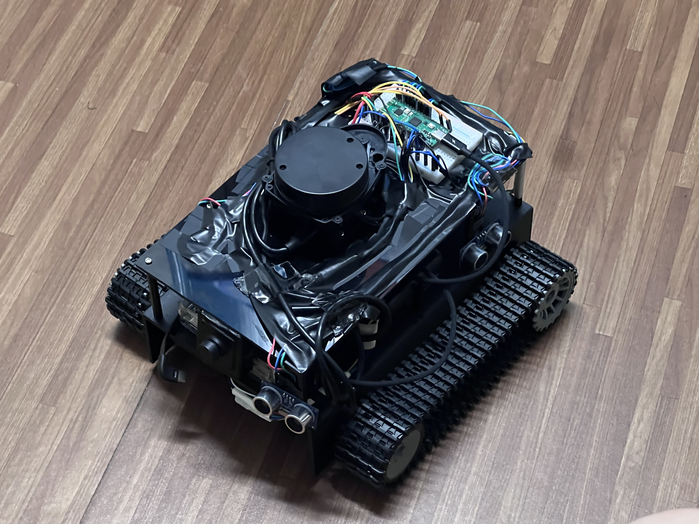
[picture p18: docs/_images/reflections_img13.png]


   Figure 13: Finished Hardware

Figure 13 shows my completed hardware. At this point, I already have my main.cpp for my micro-ROS ready to be flashed onto my 

29 Apr 26 - E-Stop Function using Ultrasonic Sensors
-----------------------------------------------------

.. raw:: html

   <figure style="text-align: center;">
   <video width="640" height="360" controls style="display: block; margin: auto;">
      <source src="../_static/reflections_vid2.mp4" type="video/mp4">
      Your browser does not support the video tag.
   </video>
   <figcaption style="color: gray; margin-top: 0.8em;">Video 2: Car stopping when 15cm from an object</figcaption>
   </figure>

Video 2 shows the simple E-stop function using my ultrasonic sensors. It will stop when it detects an object 15cm in front and behind it. 

5 May 2026 - PID Controller
-----------------------------
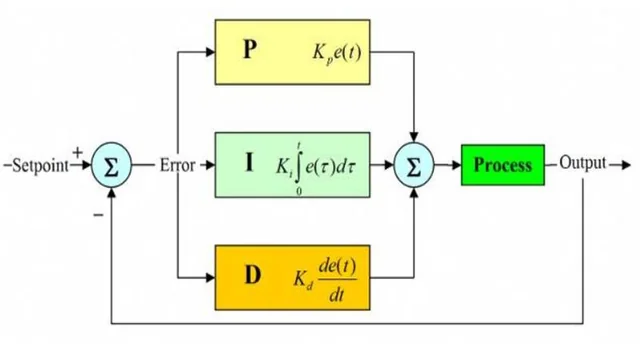
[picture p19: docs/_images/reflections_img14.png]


   Figure 14: Finished Hardware

I decided to first brush up on my concept of PID controller. Having studied this in theory and now using it irl, it was a step up. I knew that i should first begin with P, and gradually add in I and D and tune in base on how the car reacts.

When I calculate the PID values, I had to see the maximum error possible. Assuming maximum error, I can calculate the maximum PID output, and ensure that it doesn't go out of the maximum allowed value, i.e. saturation. Besides having a PID controller, we have a feedforward path that provides 80% of the motion, with PID just affect 20% of the final output by making tiny adjustments to the pwm.

I also added a slew rate that allows for smoother acceleration and deceleration.

6 May 2026 - Disaster #2
-----------------------------
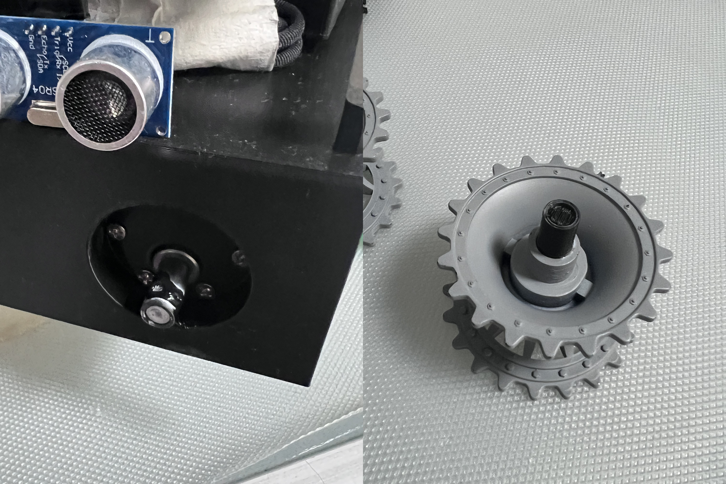
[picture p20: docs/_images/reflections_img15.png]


   Figure 15: Finished Hardware

PID controller works fine, but while moving the car, the coupler **snapped once again**. Since this entire project is self-funded and I have blasted a hole through my wallet, I had to save future costs of remaking and repurchasing this coupler and motor. Therefore, I decided to just get a full tank kit with correctly sized motors with encoders to ensure reliability. This way I can focus on what matters more, which is my SLAM and higher level algorithms. Though, what I 3D designed, the chassis and coupler, I wouldn't say its a waste of time since I did learn quite abit from this.

12 May 2026 - New Kit
-----------------------------
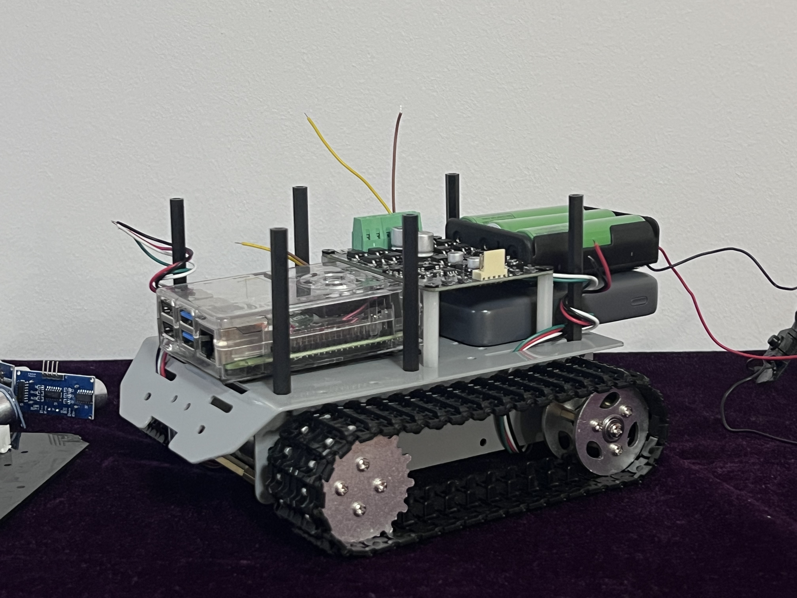
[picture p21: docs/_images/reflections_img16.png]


   Figure 16: In progress

Figure 16 shows my new chassis halfway built. Had to think about placement of sensors, how to fit my lidar on top, ensuring maximum usage of space in this smaller chassis. Also had to ensure that weight is at best equally distributed.

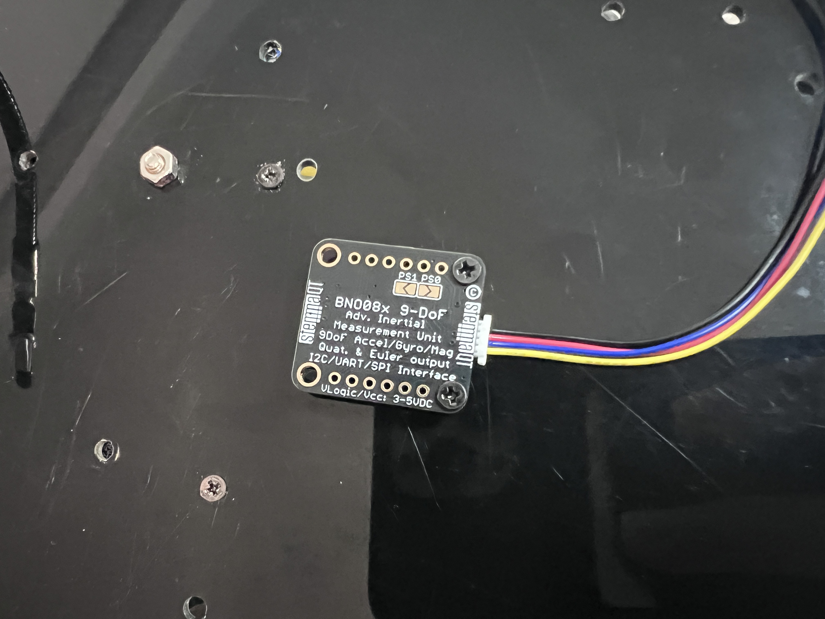
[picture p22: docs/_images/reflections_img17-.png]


   Figure 17: New IMU

Figure 17 shows a new IMU I bought. It is the BN0085 which has 9 degree of freedom. During implementation, I ensured that it is in the geometrical center of my build with z axis facing upwards, etc.

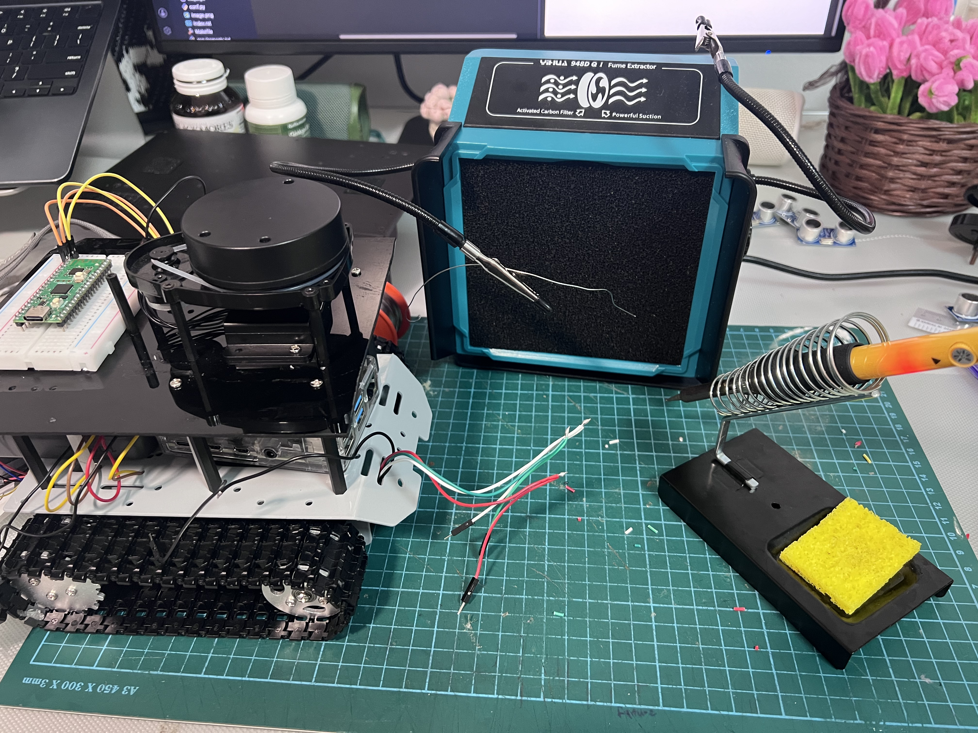
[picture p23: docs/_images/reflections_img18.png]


   Figure 18: Soldering

Figure 18 shows some soldering work that I also did with this new kit. Mainly for the motor's connections.

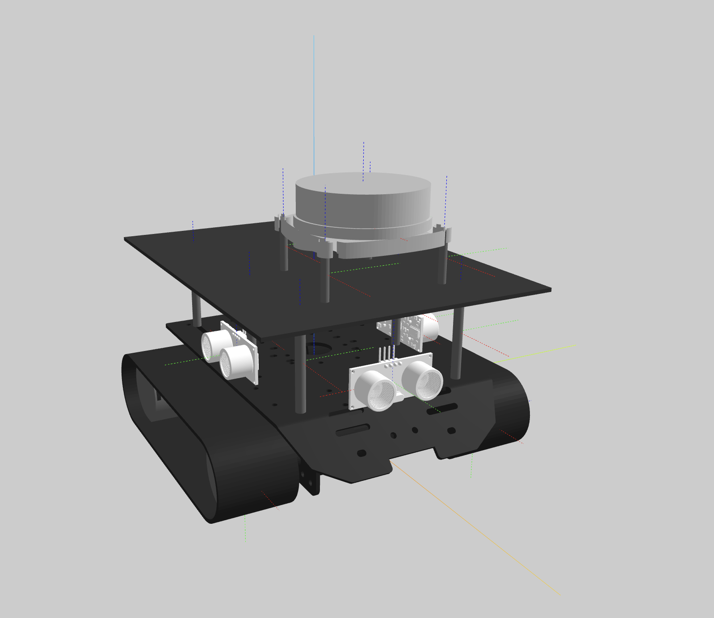
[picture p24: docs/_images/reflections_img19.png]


   Figure 19: URDF

Figure 19 shows the new model that i built as a urdf file and visualized using urdf-visualizer extension in vscode. I used provided chassis and ultrasonic sensors stl files in this design. I also added frame links in relation to base link.

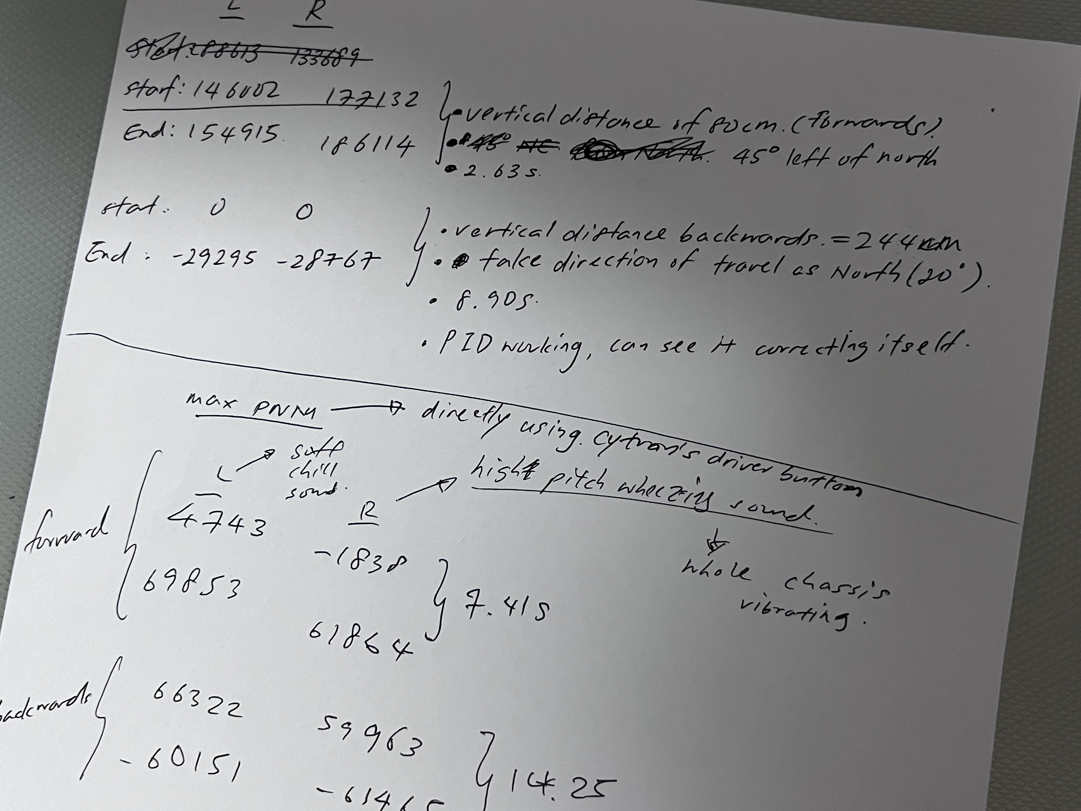
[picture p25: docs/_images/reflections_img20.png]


   Figure 20: Testing Notes

From Figure 20, we can see my testing notes. I tested the max speed and minimum duty cycle using debug code. I used encoder counts to estimate the distance and calculated the speed at max duty cycle (using timer from my stopwatch). As for minimum duty cycle, I create a debug code that steps down the duty cycle every 3 seconds, and I can manually count and see at which duty cycle the car can no longer move. However, from all these testing, I noticed the somehow the right motor is significantly weaker than the left.

20 May 2026 - Integration hell
-------------------------------

.. raw:: html

   <figure style="text-align: center;">
   <video width="640" height="360" controls style="display: block; margin: auto;">
      <source src="../_static/reflections_vid3.mp4" type="video/mp4">
      Your browser does not support the video tag.
   </video>
   <figcaption style="color: gray; margin-top: 0.8em;">Video 3: Tank forward movement biasing right</figcaption>
   </figure>

From Video 3 above, we can see that the tank is moving to the right significantly. This meant that the left motor could be stronger than the right. After checking against the published encoder ticks, I could verify this as the ticks were off by about 25%.

I thoroughly checked through my code because I thought it was a software issue, but there were nothing that caught my attention or could cause alarms.

To minimize possibility of PID implementation issue, I ran a quick debug code to test the car via the same teleop node but without PID control (so purely open loop), but the same issue arised. Nevertheless, I went straight to my Motor Driver board to test. The Cytron MDD10A has 4 built-in testing buttons that allow for current to flow directly to the motors. 

.. raw:: html

   <figure style="text-align: center;">
   <video width="640" height="360" controls style="display: block; margin: auto;">
      <source src="../_static/reflections_vid4.mp4" type="video/mp4">
      Your browser does not support the video tag.
   </video>
   <figcaption style="color: gray; margin-top: 0.8em;">Video 4: Difference in sound between left and right motor</figcaption>
   </figure>

From Video 4, we can clearly hear the difference is sound of motor when its running at max speed. This is using the bypass test buttons built-in on the motor driver. My worry is that there is a manufacturing defact of the right motor. However to be very sure, I decided to switch the motor's Output A and B on the motor driver. Meaning left motor's wiring to driver is replaced with right motor's wiring to driver, and vice versa. This is to see if the motor driver is the issue. However, after switching same thing happened, meaning motor driver was never the issue. 

.. raw:: html

   <figure style="text-align: center;">
   <video width="640" height="360" controls style="display: block; margin: auto;">
      <source src="../_static/reflections_vid5.mp4" type="video/mp4">
      Your browser does not support the video tag.
   </video>
   <figcaption style="color: gray; margin-top: 0.8em;">Video 5: Clanking sound when shaking right motor</figcaption>
   </figure>

Video 5 represents a clanking sound when shaking the right motor after removing it. This was my last straw. I decided that it was a faulty motor.

Before building

   Figure 21: Motor Close Up

Figure 21 shows the motor when I removed the gear cover. I didn't see anything odd, just poor lubrication. When I shake the motor I could still hear the clanging, and I knew it was something to do with the interal windings of the actual motor itself. But I decided not to pursue this any further and just purchase new motors (with spares cos I can't afford waiting another 1.5 weeks whenever this happens).

23 May 2026 - RViz & Gazebo
---------------------------

Before building

   Figure 22: RViz

Figure 22 shows my RViz model. Managed to set it up on my mac with much difficulty (thanks to apple sillicon).

Before building

   Figure 23: Gazebo

Figure 23 shows Gazebo setup on my mac (also a pain due to apple's sillicon). 

29 May 2026 - IMU
------------------
When i tried running the BNO085 IMU, the ROS 2 topic ``/sensors/imu`` appeared, but no data was being published to that topic. I thought it was my firmware issue, because I had to create the fully written BNO085 driver on the pico W built around the SH2 library using I2C. So I used the built-in I2C GPIO pins on the Rasberry Pi 4 for testing. 

**Here are some things I did to debug this:**

- swapped SDA/SCL pair in case cables were reversed
- confirmed 3.29V with multimeter at sensor and a lit up IMU board
- tried 2 different STEMMA QT cables
- continuity tested the blue (SDA) cable
- pulsed RST pin to force hardware reset
- used rpi4 to test if imu can be detected using ``i2c detect``

**Problem 1: I2C Timing Violation**

- SCL and SDA are both open-drain, meaning devices can only pull a line *low*
- SDA needs to be stable before SCL risess
- BNO085 uses **clock stretching** which holds SCL low to signal that its not ready yet
- the problem comes when it releases SCL after stretching, it sometimes haven't finished settling SDA
- so SDA changes too close to, or even after the clock edge
- the data is sampled mid-transition and the byte is garbage or the device never appears to acknowledge at all

**Problem 2: Pi's I2C clock-stretching bug**

- i found online that Rasberry Pi's hardware I2C has a long-standing bug where it does not honour clock stretching properly

**Solution: Swap to UART-RVC Mode**

- BNO085 supports I2C, SPI, and UART
- UART-RVC stands for Robotics Vehicle Control
- a simplified, continuous serial communication protocol designed for hardware like the BNO085/BNO086 IMUs and robot vacuum cleaners
- UART is asynchronous and does not require clock wire to get out of sync with data
- they simply agree on a baud rate (115200)
- the sensor pushes a fixed-format packet out its TX line on a timer and the Pi listens on its RX line
- RCV gives Yaw, pitch, roll, linear acc automatic streaming at a fixed rate

**I found an alternative (Software bit-banged I2C on rpi4)**

- Eventually I came back and got I2C working on the rpi4
- Im using a software bit-banged I2C bus on a free GPIO pair instead of the hardware I2C peripheral (which im been using)
- Bit-banging means the Pi manually toggles the pins in software, which correctly honours clock stretching because I'm in full control of the timing

29 May 2026 - LIDAR
--------------------
.. raw:: html

   <figure style="text-align: center;">
   <video width="640" height="360" controls style="display: block; margin: auto;">
      <source src="../_static/reflections_vid6.mp4" type="video/mp4">
      Your browser does not support the video tag.
   </video>
   <figcaption style="color: gray; margin-top: 0.8em;">Video 6: LIDAR spinning</figcaption>
   </figure>

This took me long enough, but finally I have started setting up the LIDAR and its spinning. Managed to make the LIDAR node work and I was able to see the msg being published on my lidar topic. Next was setting it up so that I can see the laser scan on rviz.

30 May 2026 - RViz2
--------------------

Before building

   Figure 24: lidar scans in rviz

Figure 24 shows my live lidar scans in my living room while my tank is stationary. The amount of satisfaction and dopamine I got from reaching this and actually seeing my lidar scan cannot be described by words. Month of grinding hardware, firmware and finally it paid off. Now I understand laying that base hardware foundation for any product/project is so important to ensure the later stages won't fall short. 

Before building

   Figure 25: added map in rviz

Figure 25 shows my live lidar scans + my map in my living room, while stationary too.

Before building

   Figure 26: alot of drift

In Figure 26, I was just driving around my living room, and it shows the drift between lidar and map. I noticed that when I move forwards in real life, the tank moved backwards in RViz. This was very odd. I went to check the axis and i realised that the red axis (+x) was facing backwards in RViz.This didn't make sense because I checked my urdf file and there was no problem.

Before building

   Figure 27: fixed axis

Figure 27 shows the problem finally fixed. The red axis which represents the positive x direction is finally pointing in the same direction as in real life. Even though the problem occured just a few lines before, I actually spent a whole gruesome day trying to debug... running through my codebase and finding anything that is causing this issue. I went through my urdf joint origins, checked my mesh files orientation, verified tf tree in rviz, re-examined how ``robot_state_publisher`` was broadcasting transforms. The whole time the answer was sitting right there. The embarrassing error was that I didn't include a 0.000 in my rpy variable ``Rotation: in RPY (degree) [0.000, -0.000, 180.000]``. This made me realised that I need to pay more attention to the little details.

Before building

   Figure 28: drift

Figure 28 shows another problem of drift. I verified that ``/odom``, ``/scan``, and ``sensors/imu`` were all actively publishing using ``ros2 topic hz``, and confirmed the EKF was outputting /odometry/filtered. I also suspected that my odom was not doing so well, at this point I tuned the EKF to weight odometry more heavily for linear velocity, since my IMU integration tends to drift on that axis. 

I also understand that my LIDAR may be giving poor results due to the characteristics of my living room, such as many dark coloured objects (sofa, piano), which abosrbs infrared light rather than reflecting it back, so the LIDAR struggles to detct them reliably. On top of that, my living room has long flat walls with no distinctive features, which makes it hard for the scan-matcher to localise accurately. I also found another issue where, my map doesn't show the rear of my bin even after moving behind it.

Before building

   Figure 29: Before (left) and After (right) of mapping a smaller area

Figure 29 shows the before and after of mapping a smaller area i created. I realised that this drastically helps with the mapping of rear of objects, since the rear of the bin is now properly shown as a fully round object. However, the drift is still a problem.

5 June 2026 - Fixing Drift
---------------------------

This drift issue is a problem. I changed maps many times and remapped them but the laser scan was always drifting. After many hours of debugging, here's what I found.

1) EKF Config File (``ekf.yaml``)

   - i disabled ``odom0 yaw`` which is encoder's angular velocity
   - because my robot is tracked, the tracks will slip when doing turns
   - adding on my tracks are plastic... so the slippage will be really bad cos the grip with the floor is really bad
   - therefore we ignore the angular velocity
   - our encoders now handle the linear velocity
   - my BNO085 gyro now handles all the rotation
   - I also ensured that ``imu0_differential: false`` is set
   - this drastically improved my drift over time since the rotation vector already has magnetometer correction baked in
   - this was because BNO085 already has its own proprietery sensor fusion

2) ``odom`` to ``base_link`` transform

   - my oodm and EKF was both trying to publish
   - I had to comment out the ``self._publish_tf(now)`` in my odom node
   - TF chain was stabilized
   - But because of this error, SLAM Toolbox fell to using pure scan matching which accumulates error overtime

3) Odometry wheelbase calibration

   - I realised after reading some random online forum that for tracked vehicles, the wheelbase is larger than the physical track to track distance
   - Therefore I had to perform the rotation test

4) IMU Heading Zeroing

   - my BNO085 boots with whatever heading it powers up in
   - it doesnt zero it, which means IMU booted facing -47 degrees and then my EKF will start with this offset
   - my ``bno085_i2c_node.py`` recorrds the first valid quartenion's yaw and applies the inverse as an offset to all subsequent readings so yaw will always start with 0

Before building

   Figure 30: Laser scans matching the walls after running around mapping the new map

Figure 30 shows the final result of a fully mapped out map with lidar scans still sticking to the walls after driving around.

Before building

Also forgot to include my live setup.

6 June 2026 - DDS Issues + Mapping
-----------------------------------

I was initially using fastDDS which is default for ROS 2 Humble. However, im using Pi as the robot, and my M2 mac for viz. FastDDS wasn't reliable with multi-machine discovery over WiFi and maybe its a skill issue, but this issue is known on reddit and also ROS community.

The community recommended CylconeDDS so i switched and I could see improvements. But after some sessions, the same issues happened again. At this point I feel like its a Robostack issue (m2 mac problems). I was thinking it was something to do with protocol level incompatibilities since rpi4's cylcloneDDS was apt installed, but mac's one was robotstack built so it was still kinda sus.

So I decided to use Foxglove Bridge. It worked wonders that's all i can say. No more issues of not finding the ROS topics anymore. The rpi4 runs a websocket server that exposes all the ROS topics over a standard wesocket protocol. On mac, I connect foxglove studio to ws://123.123.123.123:1234 using foxglove websocket protocol.

.. raw:: html

   <figure style="text-align: center;">
   <video width="640" height="360" controls style="display: block; margin: auto;">
      <source src="../_static/reflections_vid7-.mp4" type="video/mp4">
      Your browser does not support the video tag.
   </video>
   <figcaption style="color: gray; margin-top: 0.8em;">Video 7: Mapping</figcaption>
   </figure>

This is my mapping in Foxglove UI.

7 June 2026 - Nav2
---------------------------

Before building

   Figure 31: Nav2 setup in Foxglove

Figure 31 shows my setup. The first issue i faced was when i selected my goal pose and i saw the planned path. When the robot rotated, only the map would stay in place while the robot and both the goal pose and planned path would rotate together with the robot. This didn't make sense because the goal pose and planned path should be fixed to the map. 

Before building

   Figure 32: Nav2 setup in Foxglove

This was fixed by changing fixed frame AND display frame to map. Only fixed frame to map didn't work.

8 June 2026 - Past biting you
------------------------------

This was a massive issue, spent days fixing. Btw the timeline is abit off i spent many days fixing bugs between those timeline days. Please watch this video to understand the issue. The robot is the video is already trying autonomous navigation.

.. raw:: html

   <figure style="text-align: center;">
   <video width="640" height="360" controls style="display: block; margin: auto;">
      <source src="../_static/reflections_vid8.mp4" type="video/mp4">
      Your browser does not support the video tag.
   </video>
   <figcaption style="color: gray; margin-top: 0.8em;">Video 8: Fast forwarded video of Robot failing to turn the correct direction in Nav2</figcaption>
   </figure>

   This is a new remapped map so it looks slightly different. But now u can see that i selected the goal pose and the planned path is supposed to let the robot turn right, but it turned left instead. I finally found the issue after hours of debugging. I looked at my imu to make sure its pointing the right way, checking if CW rotation produced positive yaw in my topic and it did. Had to verify the differntial drive math... implementation hell. After debugging, the issue was my motor pin swapped. Hardware came back from the past to haunt me... All along my teleop node wasn't following the ROS-convention commands. However, Nav2 was sending the right commands. After swapping the motor and encoder pins in my pico firmware code and rebuilding and reflashing, it finally worked.

Another issue was my robot kept jittering, like move stop move stop at a very high frequency. I later found out its because i had my teleop node on on my phone which the ``/cmd_vel`` kept bouncing between my static (no) command and the Nav2's continuous command. It worked once i switched my teleop off.

12 June 2026 - Navigation
----------------------------

Finally, navigation worked! I have structured this in terms of nav from point A to B, and then B back to A. I noticed that B back to A takes longer because the starting pose at B is facing towards the wall so it needs to u turn which the robot finds it challenging. For the below navigation, im using Regulated Pure Pursuit (RPP) controller. I initially used Dynamic Window Approach (DWB) but its too computationally expensive (more about it in next timestep).

*-- Part 1: A to B --*
~~~~~~~~~~~~~~~~~~~~~~

.. raw:: html

   <figure style="text-align: center;">
   <video width="640" height="360" controls style="display: block; margin: auto;">
      <source src="../_static/reflections_vid11.mp4" type="video/mp4">
      Your browser does not support the video tag.
   </video>
   <figcaption style="color: gray; margin-top: 0.8em;">Video 9: A to B (Attempt 1)</figcaption>
   </figure>

Video 9 shows navigation from point A to point B (attempt 1). Notice there is slowing down near the 2 pillars.

.. raw:: html

   <figure style="text-align: center;">
   <video width="640" height="360" controls style="display: block; margin: auto;">
      <source src="../_static/reflections_vid10.mp4" type="video/mp4">
      Your browser does not support the video tag.
   </video>
   <figcaption style="color: gray; margin-top: 0.8em;">Video 10: A to B (Attempt 1 - LIVE)</figcaption>
   </figure>

Video 10 shows the same footage but live version of Video 9, from A to B (attempt 1). Same no slowing at the 2 pillars.

Below is attempt 2 from A to B.

.. raw:: html

   <figure style="text-align: center;">
   <video width="640" height="360" controls style="display: block; margin: auto;">
      <source src="../_static/reflections_vid9-.mp4" type="video/mp4">
      Your browser does not support the video tag.
   </video>
   <figcaption style="color: gray; margin-top: 0.8em;">Video 11: A to B (Attempt 2)</figcaption>
   </figure>

Video 11 shows navigation from point A to point B (attempt 2). Notice how it slows down near the pillars.

.. raw:: html

   <figure style="text-align: center;">
   <video width="640" height="360" controls style="display: block; margin: auto;">
      <source src="../_static/reflections_vid12.mp4" type="video/mp4">
      Your browser does not support the video tag.
   </video>
   <figcaption style="color: gray; margin-top: 0.8em;">Video 12: A to B (Attempt 2 - LIVE)</figcaption>
   </figure>

Video 12 shows navigation from point A to point B (attempt 2). Likewise, you can see how it slows down near the pillars. This is because I used ``use_regulated_linear_velocity_scaling: true``.

Now, lets look at the B to A motion.

*-- Part 2: B to A --*
~~~~~~~~~~~~~~~~~~~~~~~

.. raw:: html

   <figure style="text-align: center;">
   <video width="640" height="360" controls style="display: block; margin: auto;">
      <source src="../_static/reflections_vid15.mp4" type="video/mp4">
      Your browser does not support the video tag.
   </video>
   <figcaption style="color: gray; margin-top: 0.8em;">Video 13: B to A (Attempt 1)</figcaption>
   </figure>

Video 13 shows successful navigation from point B to point A but it took really long for it to get out. 

.. raw:: html

   <figure style="text-align: center;">
   <video width="640" height="360" controls style="display: block; margin: auto;">
      <source src="../_static/reflections_vid14.mp4" type="video/mp4">
      Your browser does not support the video tag.
   </video>
   <figcaption style="color: gray; margin-top: 0.8em;">Video 14: B to A (Attempt 1 - LIVE)</figcaption>
   </figure>

Video 14 shows the same point B to A as video 13 but live, and u can see how it really moves and "thinks" to get out of the sticky situation. I find this so intriguing.

Now move on to after optimization.

.. raw:: html

   <figure style="text-align: center;">
   <video width="640" height="360" controls style="display: block; margin: auto;">
      <source src="../_static/reflections_vid16.mp4" type="video/mp4">
      Your browser does not support the video tag.
   </video>
   <figcaption style="color: gray; margin-top: 0.8em;">Video 15: B to A (Attempt 2)</figcaption>
   </figure>

Video 15 shows successful navigation from point B to point A and it took way lesser time to get out. 

.. raw:: html

   <figure style="text-align: center;">
   <video width="640" height="360" controls style="display: block; margin: auto;">
      <source src="../_static/reflections_vid17.mp4" type="video/mp4">
      Your browser does not support the video tag.
   </video>
   <figcaption style="color: gray; margin-top: 0.8em;">Video 16: B to A (Attempt 2 - LIVE)</figcaption>
   </figure>

Video 16 shows the same point B to A as video 13 but live. You can see how it got out of the situation quicker and in a different way. This is because of a particular change i made in config, which was ``movement_time_allowance:``, this is a progress checker timeout where robot must fail to make progress for 20 seconds before Nav2 triggers recovery behaviours like spin and backup which was exactly what we can see.

14 June 2026 - Obstacle Avoidance
---------------------------------

For this part, I used both DWB and RPP and we can see how the per-cycle compute demands of DWB really couldn't be met by my rasberry pi 4. RPP on the other hand doesn't need to do trajectory sampling, that's why its so efficient. Planner also kept at 2Hz and it ran stably with RPP. For obstacle avoidance, I split it up into Far Range and Close Range. Close range being adding the obstacle last minute right in front of the robot. Far Range is adding the obstacle when the robot is still far away, so it has time to replan its route.

*-- DWB (Far Range) --*
~~~~~~~~~~~~~~~~~~~~~~~

.. raw:: html

   <figure style="text-align: center;">
   <video width="640" height="360" controls muted style="display: block; margin: auto;">
      <source src="../_static/dwb_far_range.mp4" type="video/mp4">
      Your browser does not support the video tag.
   </video>
   <figcaption style="color: gray; margin-top: 0.8em;">Video 17: DWB, Far range, Foxglove Studio</figcaption>
   </figure>

Video 17 shows foxglove view of me placing the obstacle early on. Using DWB for this and we can see at the end the robot stopped. Near the goal, the ``RotateToGoal`` and ``GoalAlign`` critics kick in. The additional scoring when the robot is trying to start orienting to the final heading, caused it to miss the cycle deadline and the recovery comes in and the loop continues. This is why the robot appears to stop nearing the end because it requires additional orienting and heading towards final pose. This is consistent.

.. raw:: html

   <figure style="text-align: center;">
   <video width="640" height="360" controls muted style="display: block; margin: auto;">
      <source src="../_static/dwb_far_range_real.mp4" type="video/mp4">
      Your browser does not support the video tag.
   </video>
   <figcaption style="color: gray; margin-top: 0.8em;">Video 18: DWB, Far range, Real life</figcaption>
   </figure>

Video 18 shows the live version of video 17.

*-- DWB (Close Range) --*
~~~~~~~~~~~~~~~~~~~~~~~~~

.. raw:: html

   <figure style="text-align: center;">
   <video width="640" height="360" controls muted style="display: block; margin: auto;">
      <source src="../_static/dwb_close_range.mp4" type="video/mp4">
      Your browser does not support the video tag.
   </video>
   <figcaption style="color: gray; margin-top: 0.8em;">Video 19: DWB, Close range, Foxglove Studio</figcaption>
   </figure>

Here in Video 19, we can see it behaves in close object avoidance. Same issue when nearing the end.

.. raw:: html

   <figure style="text-align: center;">
   <video width="640" height="360" controls muted style="display: block; margin: auto;">
      <source src="../_static/dwb_close_range_real.mp4" type="video/mp4">
      Your browser does not support the video tag.
   </video>
   <figcaption style="color: gray; margin-top: 0.8em;">Video 20: DWB, Close range, Real life</figcaption>
   </figure>

Video 20 shows the live version of video 19.

*-- RPP (Far Range) --*
~~~~~~~~~~~~~~~~~~~~~~~

.. raw:: html

   <figure style="text-align: center;">
   <video width="640" height="360" controls muted style="display: block; margin: auto;">
      <source src="../_static/rpp_far_range.mp4" type="video/mp4">
      Your browser does not support the video tag.
   </video>
   <figcaption style="color: gray; margin-top: 0.8em;">Video 21: RPP, Far range, Foxglove Studio</figcaption>
   </figure>

Now with RPP, we can see the stark difference in Video 21. The moment I placed the object when its far away, the new path was calculated and planned almost instantly. RPP just follows that new path. No issue at the end.

.. raw:: html

   <figure style="text-align: center;">
   <video width="640" height="360" controls muted style="display: block; margin: auto;">
      <source src="../_static/rpp_far_range_real.mp4" type="video/mp4">
      Your browser does not support the video tag.
   </video>
   <figcaption style="color: gray; margin-top: 0.8em;">Video 22: RPP, Far range, Real life</figcaption>
   </figure>

Video 22 shows the live version of Video 21.

*-- RPP (Close Range) --*
~~~~~~~~~~~~~~~~~~~~~~~~~

.. raw:: html

   <figure style="text-align: center;">
   <video width="640" height="360" controls muted style="display: block; margin: auto;">
      <source src="../_static/rpp_close_range.mp4" type="video/mp4">
      Your browser does not support the video tag.
   </video>
   <figcaption style="color: gray; margin-top: 0.8em;">Video 23: RPP, Close range, Foxglove Studio</figcaption>
   </figure>

Here in Video 23, we can see a close range quick object avoidance. See Video 24 for better understanding of what's happening.

.. raw:: html

   <figure style="text-align: center;">
   <video width="640" height="360" controls muted style="display: block; margin: auto;">
      <source src="../_static/rpp_close_range_real.mp4" type="video/mp4">
      Your browser does not support the video tag.
   </video>
   <figcaption style="color: gray; margin-top: 0.8em;">Video 24: RPP, Far range, Real life</figcaption>
   </figure>

Video 24 shows the live version of video 23. We can see how the robot is reacting fast to my attempts to block its path.

*-- Stress Test --*
~~~~~~~~~~~~~~~~~~~

.. raw:: html

   <figure style="text-align: center;">
   <video width="640" height="360" controls muted style="display: block; margin: auto;">
      <source src="../_static/stress_test.mp4" type="video/mp4">
      Your browser does not support the video tag.
   </video>
   <figcaption style="color: gray; margin-top: 0.8em;">Video 25: Stress Test</figcaption>
   </figure>

This stress test is my exaggerated attempt of trying to block the robot, but the RPP + NavFn combo is just so much better, at least on the CPU starved RPI4. Watch Video 26 to see my pov.

.. raw:: html

   <figure style="text-align: center;">
   <video width="640" height="360" controls muted style="display: block; margin: auto;">
      <source src="../_static/stress_test_real.mp4" type="video/mp4">
      Your browser does not support the video tag.
   </video>
   <figcaption style="color: gray; margin-top: 0.8em;">Video 26: Stress Test, Real Life</figcaption>
   </figure>

Video 26 is the live version of video 25.

Conclusion
-----------

This journey was surely a long one. I managed to learn so much, from C++, python, to Robotics fundamentals, math algorithms, ROS 2, slam, navigation, obstacle avoidance, electronics, 3d printing, modelling using fusion 360 and computer networks, it was surely a fruitful one indeed. Now I will be focusing on VLA since thats where my FYP and current trend is heading for Modern Robotics. This gave me a glimpse of what the mature age of "old-school" robotics was like, at least for autonomous navigation, obstacle avoidance and localization. I still having much to learn, anyways on to the next chapter!

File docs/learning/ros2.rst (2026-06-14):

ROS 2 Notes
==================

See also: *Reflections*

1. Core Architecture & Concepts
-------------------------------

.. list-table::
    :header-rows: 1
    :widths: 20 80

    * - Term
      - Definition

    * - Nodes
      - A process that performs a specific task. Nodes are child classes inheriting from the ROS parent ``Node`` class. Each node runs in its own isolated runtime environment and can be written in Python, C++, or almost any other supported language.

    * - Packages
      - The basic unit of organization in ROS. It contains code (``package.xml``, ``CMakeLists.txt``, ``setup.py`` source files) needed to run something.``colcon build`` uses ``package.xml`` (similar to a ``requirements.txt``) to build the package.

    * - Messages
      - The strongly typed communication “language” (strings, ints, floats, arrays)
        passed between nodes.

    * - Interfaces
      - The blueprint or format of a message. It defines the programming API for data
        received/sent via topics or services. ROS provides pre-defined interfaces,
        but custom ones can be created.

    * - Topics
      - Named, asynchronous communication channels using a Publish–Subscribe model.
        A node publishes a message to a topic, and all subscribing nodes receive it.

    * - Services
      - Synchronous communication channels using a Request–Response model. A client
        node sends a request to a server node, which executes a task and returns
        a response.

    * - Callbacks
      - Functions that ROS will execute when an event occurs (e.g., message
        received, timer fired). This keeps ROS 2 code modular.

    * - Timers
      - Mechanisms integrated with the ROS executor that run a specific callback
        function at a defined interval (e.g., “run every 10 ms”).

    * - Parameters
      - Named configuration settings stored within a node (int, float, bool, string,
        list). They allow behavior changes without altering code and can be set via
        command line, YAML, or launch files.

    * - Logging
      - Structured node status output (DEBUG, INFO, WARN, ERROR, FATAL) that replaces
        raw ``print()`` calls. Logs can be routed to the terminal, files, or
        ``/rosout`` for centralized filtering and monitoring.

    * - twist_mux
      - A node that subscribes to multiple velocity topics and outputs values based
        on configured priority (typically handled via a YAML file).

2. Coordinate Systems & TF2 (Transformations)
---------------------------------------------

* **Link:** A named, physical fixed body part of your robot (e.g., chassis, wheel, sensor mount).
* **Frame:** A local coordinate system attached to a link, complete with its own origin (0,0,0) and directional axes (x,y,z). Note that abstract frames like ``odom`` and ``map`` do not have physical hardware attached.
* **URDF (Unified Robot Description Format):** An XML file that defines the fixed physical offsets between your robot's frames.

The TF Tree
~~~~~~~~~~~

- TF2 bridges coordinate systems together
- Tt is literally like a tree that connects different branches (links) together
- It chains transforms to translate measurements from one frame to another

.. code-block:: text

  odom (fixed to world at startup)
  └── base_link (moving with the robot)
      ├── lidar_link
      ├── wheel_left_link
      └── wheel_right_link

Key TF2 Components
~~~~~~~~~~~~~~~~~~

* **odom (Node & Frame):** The base reference frame is anchored at the robot's starting position. The ``odom`` node acts as a generic TF2 broadcaster, publishing the transform (position x, y and rotation theta) between ``base_link`` (current position) and ``odom`` (start) to the ``/tf`` topic.
* **base_link:** The child frame moving with the robot's body. Physical sensors (``lidar_link``) are children of ``base_link``. Therefore, lidar_link is the grandchild of base_link.
* **TF2 Library:** Contains broadcasters, a buffer, and listeners. The buffer subscribes to both ``/tf`` (dynamic movement) and ``/tf_static`` (fixed physical offsets).
* **robot_state_publisher**: It does publish the fixed, non-moving offsets (like base_link to lidar_link) to /tf_static once at startup. It then constantly listens to the angles of the moving joints (wheels), uses the URDF to calculate complex 3D math (Forward Kinematics), and continuously publishes the live coordinates of the moving parts to /tf.
* **joint_state_publisher**: It publishes those "The left wheel is currently rotated at 45 degrees" messages continuously to a specific topic called /joint_states. On a real robot, the physical motor encoders do this job. When simulating or testing, this node fakes the encoder data.
* **RViz2**: RViz2 reads the tank.urdf file first so it knows what the physical 3D .stl meshes look like. Then, it listens to the math coming from both /tf (for moving parts) and /tf_static (for fixed parts) to know exactly where in the virtual world to draw those meshes, so that we can visualize it in real-time.

3. Understanding Packages
--------------------------

Understanding packages and its contents.

* ``colcon build``: colcon is like the main universal way of building packages regardless of the type of source files (python or C++)
* ``ament``: ``ament_python`` or ``ament_cmake`` are build types (specific ways we can build), colcon sees this and understands which ways we want to build our package
* ``ament_python``: always contains python source files and a config.py files, sometimes containing a setup.cfg
* ``ament_cmake``: usually contains C++ source files, but also used for "resource-only" packages that hold models, maps, custom messages, or configuration files

.. code-block:: xml

  <!-- Found in the packages.xml file -->

  <!-- For C++ -->
  <export>
    <build_type>ament_cmake</build_type>
  </export>

  <!-- For python -->
  <export>
  <build_type>ament_python</build_type>
  </export>

1) ``package.xml``

- just a ID card and dependency checklist
- ``<buildtool_depend>`` tells ROS 2 what software is needed to actually compile the package, python (an interpreted language) packages doesn't need this because it doesn't get compiled unlike C++, it simply gets copied over to /install therefore we dont need this, C++ packages explicitly requires this to be stated in packages.xml cos it needs to be compiled into machines binary code
- ``<exec_depend>`` is called *Execution Dependencies* which is what our launch files depend on when we are running it
- ``<test_depend>`` are the dependencies we require to test our code, such as ``pytest``, ``flake8``, and ``pep257`` which are all standard Python code linters (tools that check your code for formatting errors)
- ``<build_type>ament_python</build_type>`` is the tag that ``colcon`` requires to know to look for ``CMakeLists.txt`` or ``config.py`` on how to handle to installation (into /install)

2) ``CMakeLists.txt``

- ``install(DIRECTORY ...)`` This is essentially a "copy-paste" command for the build process. When you run colcon build, ROS 2 doesn't use the files directly from your source code folder. It needs to put them in a central "install space" so the rest of the robot system can find them.
- ``DESTINATION share/${PROJECT_NAME}/)`` This is where those folders get pasted. In ROS 2, description files, launch files, and models are standardly placed in the share/ directory of the installed package.
- ``project(...)`` This gives your package a name. It also creates a handy background variable called ${PROJECT_NAME}

3) ``setup.py``

- ``packages=find_packages(exclude=['test'])`` find packages is a python tool that automatically searches package directory and grabs all the python code so they can be installed
- ``exclude=['test']`` intentionally ignores test/ folders so that testing scripts don't get installed onto robot
- ``data_files=[('share/ament_index/resource_index/packages', ['resource/' + package_name]), ('share/' + package_name, ['package.xml']),],`` first tuple puts a blank marker file deep inside ROS2 system. when we type ``ros2 pkg list``, ROS2 seaches this exact folder to know the existing packages, second tuple copies package.xml file into share/rc_car_teleop installation folder so ROS2 can read the dependencies at runtime
- ``install_requires=['setuptools'], tests_require=['pytest'],`` tells the system it needs ``setuptools`` library to build the package, and the ``pytest`` package to run tests

.. code-block:: python

  entry_points={
      'console_scripts': [
          'teleop          = rc_car_teleop.teleop:main',
          'odometry        = rc_car_teleop.robot_core.odom:main',
          'lidar_processor = rc_car_teleop.robot_core.lidar_processor:main'
      ],
  },

- teleop: This is the name of the executable to create. we use it when we run the command: ``ros2 run rc_car_teleop teleop``.
- rc_car_teleop.teleop:main: This is the path to the code. It tells ROS 2, "Look inside the rc_car_teleop folder, find the teleop.py script, and execute the function called main()."

4) ``launch.py``

- split into 3 parts: imports, generator function, execution/return
- allows us to ros2 launch my_package my_launch.py

**Full Code Block**

.. code-block:: python

  # ==========================================
  # PART 1: THE IMPORTS
  # ==========================================
  from launch import LaunchDescription
  from launch_ros.actions import Node

  # ==========================================
  # PART 2: THE GENERATOR FUNCTION
  # ==========================================
  def generate_launch_description():
    
    # 1. Define your first node (e.g., the joystick teleop)
    teleop_node = Node(
        package='rc_car_teleop',     # The package name (from package.xml)
        executable='teleop',         # The executable name (from setup.py entry_points)
        name='joystick_teleop',      # What to call this specific instance of the node
        output='screen',             # Print the node's output to this terminal
        parameters=[
            {'max_speed': 2.5}       # Inject parameters directly!
        ]
    )

    # 2. Define your second node (e.g., the lidar processor)
    lidar_node = Node(
        package='rc_car_teleop',
        executable='lidar_processor',
        name='lidar_processor',
        output='screen',
        remappings=[
            ('/scan', '/scan_filtered')  # Change topic names on the fly
        ]
    )

    # ==========================================
    # PART 3: THE EXECUTION / RETURN
    # ==========================================
    # ROS 2 expects this function to return a LaunchDescription object
    # containing a list of all the actions/nodes you want to start.
    return LaunchDescription([
        teleop_node,
        lidar_node
    ])

**Part 1: imports**

.. code-block:: python

  from launch import LaunchDescription
  from launch_ros.actions import Node

Always need to import these.

**Part 2: generator function**

.. code-block:: python

  def generate_launch_description():
    
    # 1. Define your first node (e.g., the joystick teleop)
    teleop_node = Node(
        package='rc_car_teleop',     # The package name (from package.xml)
        executable='teleop',         # The executable name (from setup.py entry_points)
        name='joystick_teleop',      # What to call this specific instance of the node
        output='screen',             # Print the node's output to this terminal
        parameters=[
            {'max_speed': 2.5}       # Inject parameters directly!
        ]
    )

    # 2. Define your second node (e.g., the lidar processor)
    lidar_node = Node(
        package='rc_car_teleop',
        executable='lidar_processor',
        name='lidar_processor',
        output='screen',
        remappings=[
            ('/scan', '/scan_filtered') # Change topic names on the fly
        ]
    )

exact function name is mandatory, when we run ``ros2 launch``, the ros2 system searches the python script specifically for a function called ``generate_launch_description()``. The ``Node`` block references everything from previous files.

**Part 3: return**

.. code-block:: python

  return LaunchDescription([
          teleop_node,
          lidar_node
      ])

bundle all the nodes, scripts, and configs defines into a single list and pass it to ``LaunchDescription([...])``. When this object is returned, ROS2 takes over and starts spinning up the processes.

4. SLAM and Mapping
-------------------

SLAM is Simultaneous Localization and Mapping. The robot builds a map of
an unknown space while working out where it is inside that map at the same time.
On the tank I use the ``slam_toolbox`` package in synchronous mode
(``sync_slam_toolbox_node``).

What slam_toolbox does
~~~~~~~~~~~~~~~~~~~~~~~

* **Input**: the laser scans on ``/scan`` and the robot's rough pose from the ``odom`` to ``base_link`` transform
* **Scan matching**: it lines each new scan up against the map so far to correct the pose
* **Output**: an occupancy grid (the map) on ``/map``, plus the ``map`` to ``odom`` transform

The map, odom and base_link frames
~~~~~~~~~~~~~~~~~~~~~~~~~~~~~~~~~~~~

While mapping, the transform chain looks like this, with the node that owns each link:

.. code-block:: text

  map        <- slam_toolbox          (scan matching correction)
   |
  odom       <- EKF                   (encoders + IMU fused)
   |
  base_link  <- EKF
   |
  lidar_link, imu_link, ...           <- robot_state_publisher (from the URDF)

* **map to odom**: the slow correction from scan matching, which cancels long term drift
* **odom to base_link**: the fast, smooth motion estimate from the EKF
* Only one node should publish a given transform. Both my odom node and the EKF were publishing ``odom`` to ``base_link``, so I let the EKF own it and turned off the odom node's broadcast

The EKF (robot_localization)
~~~~~~~~~~~~~~~~~~~~~~~~~~~~~

The EKF fuses ``/odom`` (encoders) and ``/sensors/imu`` (BNO085) into a smoother
``/odometry/filtered`` and publishes the ``odom`` to ``base_link`` transform. Key
choices in ``ekf.yaml``:

* **Encoders for linear velocity only**: the plastic tracks slip when turning, so the encoder yaw is not trustworthy, and I stop fusing the encoder angular velocity
* **IMU for all rotation**: the BNO085 rotation vector is already fused with the magnetometer on the chip, so I trust it for yaw and set ``imu0_differential: false`` to use its absolute heading
* **Heading zeroing**: the BNO085 boots facing a random direction, so ``bno085_i2c_node`` saves the first yaw and subtracts it from every later reading, which makes yaw always start at zero

Talking to the laptop (DDS)
~~~~~~~~~~~~~~~~~~~~~~~~~~~~

The Pi runs the robot and the laptop runs the viewer, so the two have to talk over WiFi.

* **Fast DDS**: the ROS 2 Humble default, which kept dropping topics between machines over WiFi
* **Cyclone DDS**: more reliable for a while, then the same trouble came back
* **Foxglove Bridge**: the fix I settled on, where the Pi serves every topic over a websocket and Foxglove Studio connects to it from the laptop

5. Nav2 and Navigation
----------------------

Nav2 is the ROS 2 navigation stack. Give it a map and a goal pose, and it plans a
path and drives the robot there while avoiding obstacles.

The Nav2 nodes
~~~~~~~~~~~~~~

* **map_server**: loads the saved map
* **amcl**: localizes the robot on the map with a particle filter
* **planner_server**: plans the global path to the goal
* **controller_server**: follows the path and puts out the velocity command
* **velocity_smoother**: smooths the controller output before it goes out
* **behavior_server**: runs the recovery moves like spin and back up
* **bt_navigator**: the behaviour tree that ties planning, following and recovery together
* **lifecycle_manager**: brings all the Nav2 nodes up in order, which the Pi needs extra time for

How a goal flows
~~~~~~~~~~~~~~~~

.. code-block:: text

  goal in Foxglove
    -> /goal_pose
    -> goal_pose_relay        (zeroes the timestamp)
    -> /goal_pose_relayed
    -> bt_navigator -> planner_server + controller_server
    -> /cmd_vel_raw -> velocity_smoother
    -> /nav2/cmd_vel
    -> twist_mux -> /cmd_vel
    -> the Pico

* **goal_pose_relay**: Nav2 kept transforming the goal at its original timestamp, which fell out of the TF buffer during slow recoveries and broke replanning, so this node zeroes the stamp and the planner then uses the latest transform
* **twist_mux**: picks one velocity source by priority, where teleop (100) beats Nav2 (50) so I can always take over

Controllers: RPP vs DWB
~~~~~~~~~~~~~~~~~~~~~~~~

* **DWB (Dynamic Window Approach)**: samples many possible trajectories each cycle and scores them with critics. Powerful but heavy, and too expensive for the Pi 4. Near the goal its ``RotateToGoal`` and ``GoalAlign`` critics pushed each cycle past its deadline, so the robot stalled and dropped into recovery
* **RPP (Regulated Pure Pursuit)**: no trajectory sampling, it just follows the planned path. Light enough to run smoothly with the planner held at 2 Hz, so this is the one I use
* **use_regulated_linear_velocity_scaling**: slows the robot near tight spots, which is why it eases past the pillars
* **progress checker timeout**: the robot has to fail to make progress for a set time before recovery kicks in, so it does not give up too early

Obstacle avoidance
~~~~~~~~~~~~~~~~~~

* **Far range**: the obstacle is placed early, so there is time to plan a fresh route around it
* **Close range**: the obstacle is dropped right in front, so the robot has to react at the last second
* On the Pi 4, RPP with the NavFn planner handled both cases far better than DWB, drawing a new path almost instantly when the path was blocked

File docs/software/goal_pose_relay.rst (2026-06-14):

Goal Pose Relay
===============

.. automodule:: rc_car_teleop.goal_pose_relay
   :members:

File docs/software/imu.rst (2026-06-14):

IMU
===

The tank reads its BNO085 IMU on the Raspberry Pi. There are two nodes for it.
The I2C node is the one used during normal running. The RVC node is an option
that reads the same sensor over a serial connection.

.. automodule:: rc_car_teleop.robot_core.bno085_i2c_node
   :members:

.. automodule:: rc_car_teleop.robot_core.bno085_rvc_node
   :members:

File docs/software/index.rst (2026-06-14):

Software
========

This section covers the ROS 2 software that runs on the Raspberry Pi 4. It
starts with a short overview of the system, then gives the API for each Python
node. The API pages are generated from the docstrings in the source, so they
stay in sync with the code.

Overview
--------

.. toctree::
    :maxdepth: 1

    ros2_overview

Python API
----------

.. toctree::
    :maxdepth: 1

    odom
    lidar_processor
    teleop
    imu
    goal_pose_relay

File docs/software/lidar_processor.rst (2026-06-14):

Lidar Processor
===============

.. automodule:: rc_car_teleop.robot_core.lidar_processor
   :members:

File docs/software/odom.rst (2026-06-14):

Odometry
========

.. automodule:: rc_car_teleop.robot_core.odom
   :members:

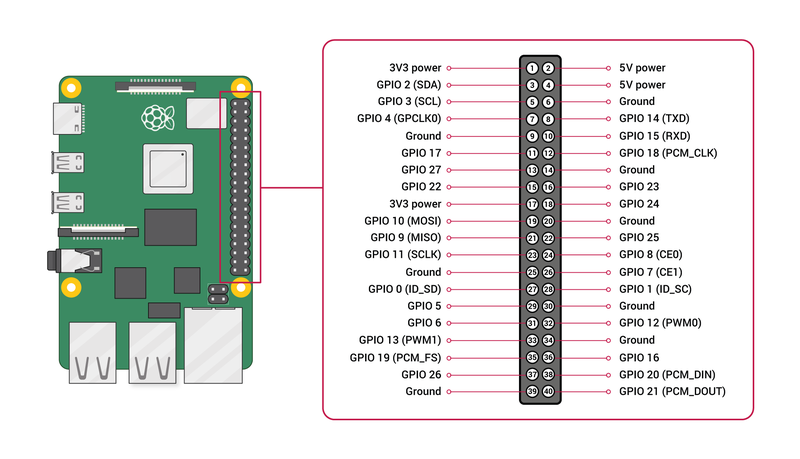
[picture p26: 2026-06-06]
docs/hardware/build_reference/devices/RPI4B/800px-GPIO-Pinout-Diagram-2.png

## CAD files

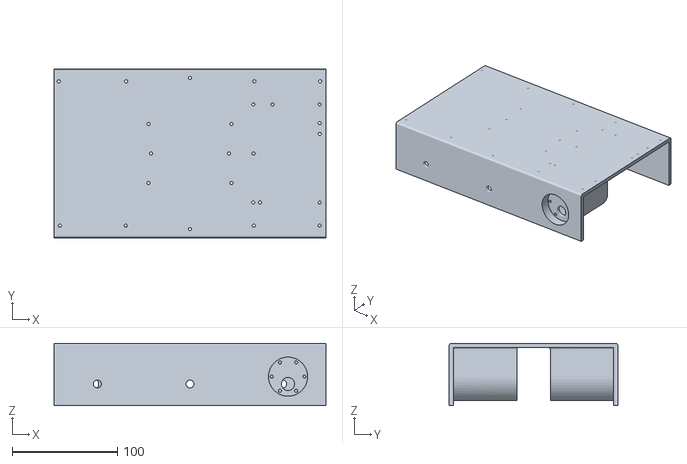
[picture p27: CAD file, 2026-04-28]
software/ros2_ws/src/tank_description/meshes/full_chassis.stl
258.0 x 160.0 x 59.0

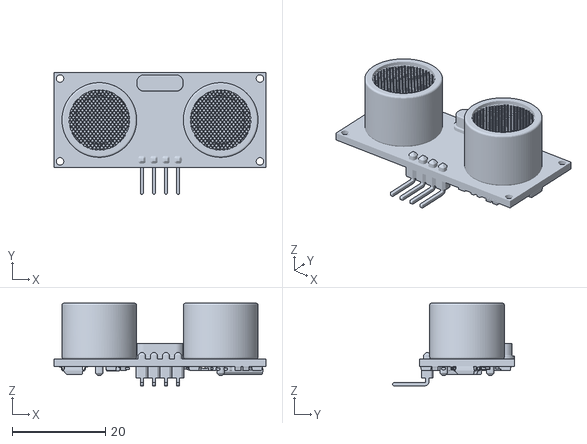
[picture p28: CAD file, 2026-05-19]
software/ros2_ws/src/tank_description/meshes/ultrasonic_sensor.stl
45.4 x 26.1 x 17.7

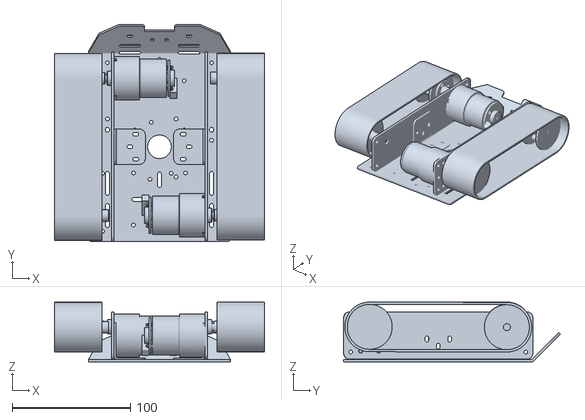
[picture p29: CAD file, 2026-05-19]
software/ros2_ws/src/tank_description/meshes/new_chassis.stl
177.6 x 183.4 x 50.7

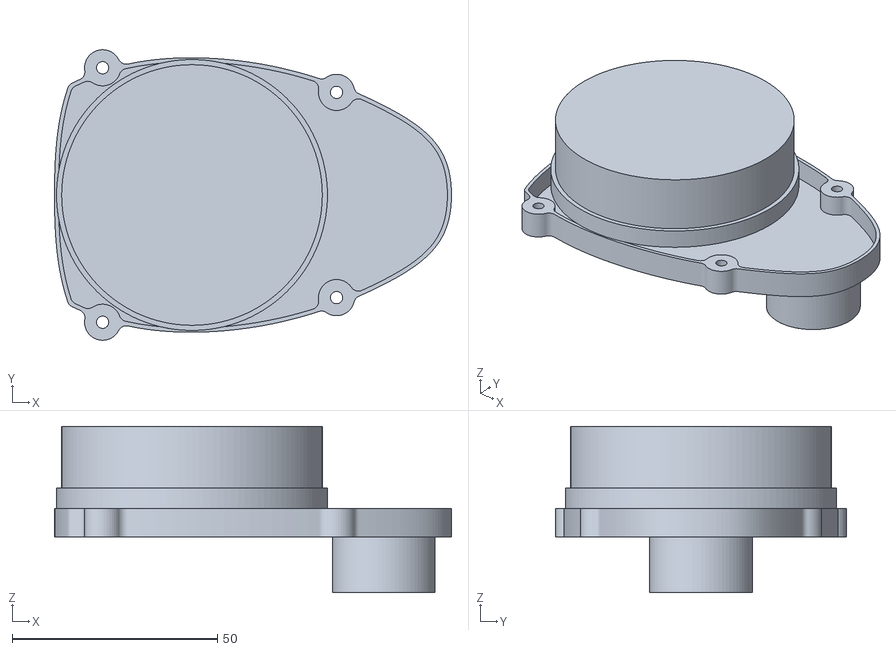
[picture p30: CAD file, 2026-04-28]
software/ros2_ws/src/tank_description/meshes/YDLIDAR_X3Pro.stl
96.7 x 70.8 x 40.5

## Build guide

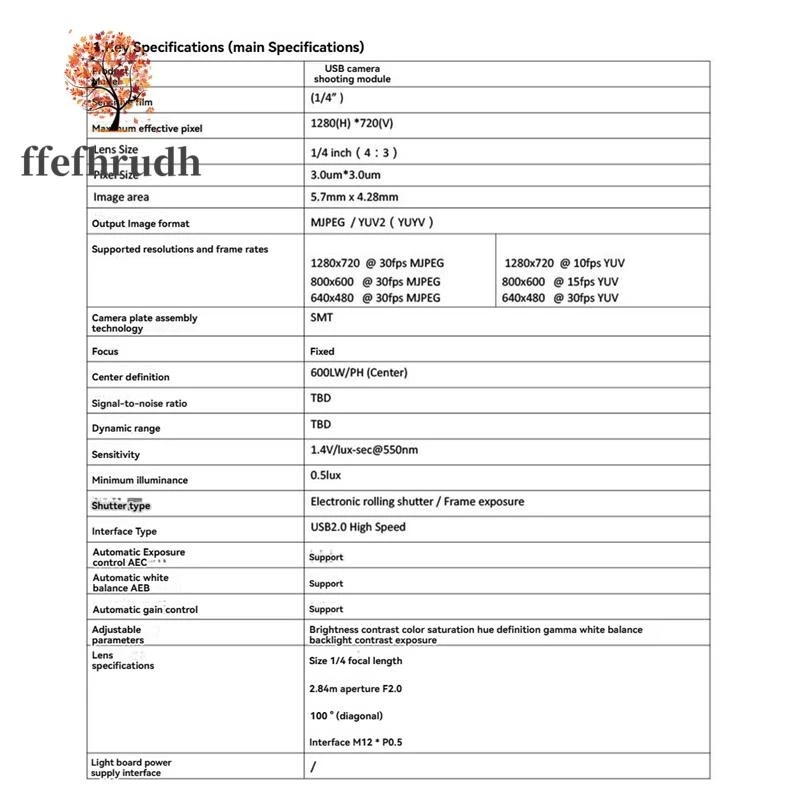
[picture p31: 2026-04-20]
docs/hardware/build_reference/devices/OV9732/img_1.webp

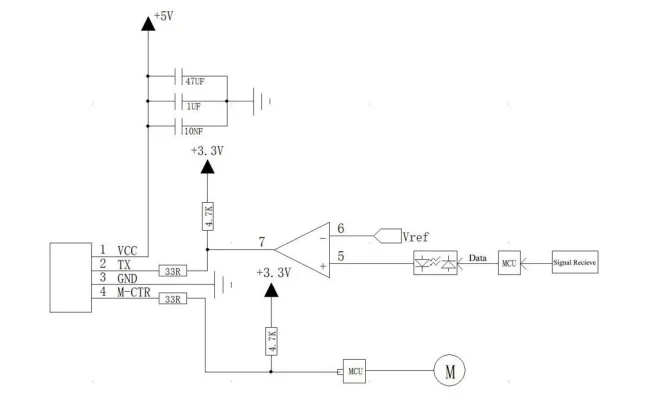
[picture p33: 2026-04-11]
docs/hardware/build_reference/devices/YD_Lidar_X3Pro/img_3.webp

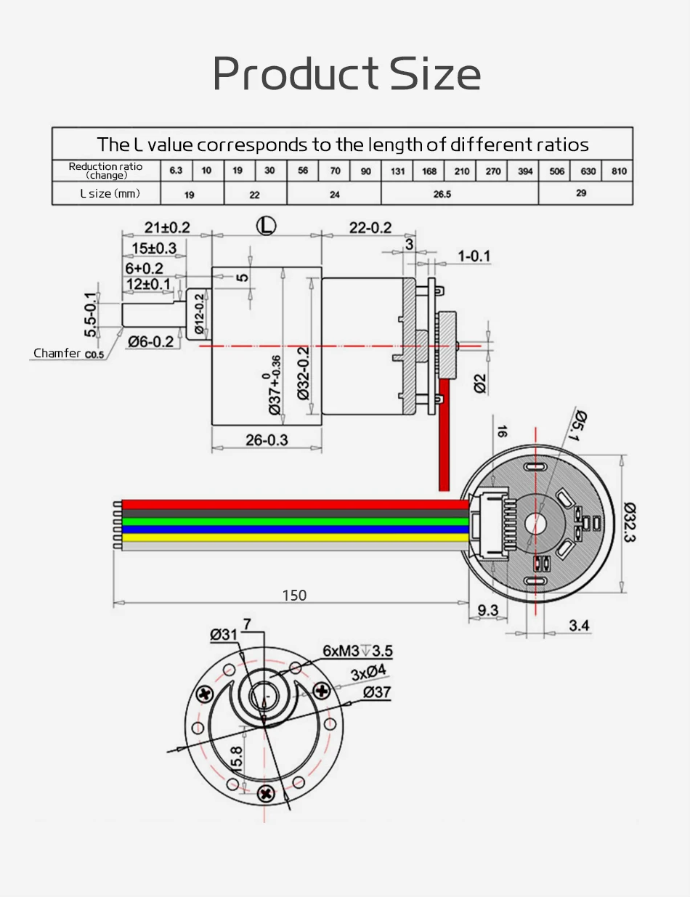
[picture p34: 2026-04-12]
docs/hardware/build_reference/devices/JGB37-520-12V-60RPM/img1.webp

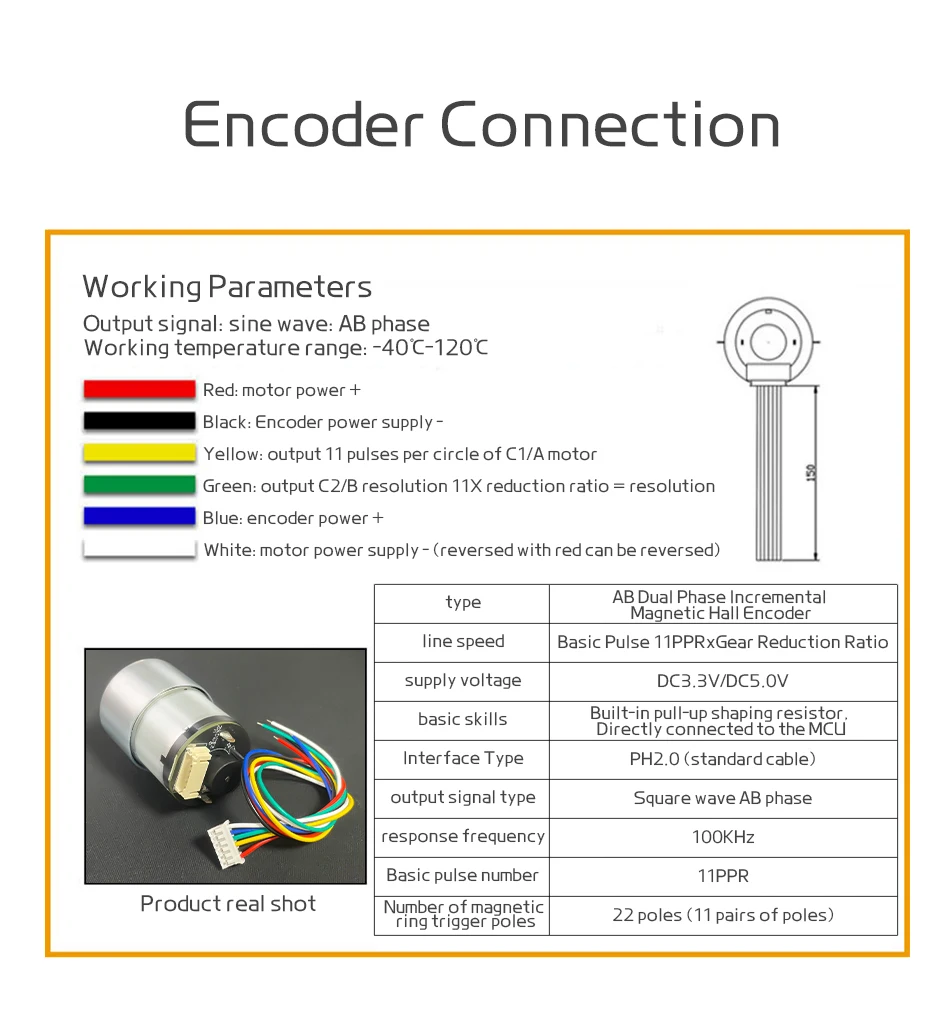
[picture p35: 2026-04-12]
docs/hardware/build_reference/devices/JGB37-520-12V-60RPM/img2.webp

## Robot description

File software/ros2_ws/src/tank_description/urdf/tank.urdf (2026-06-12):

<?xml version="1.0"?>
<robot name="my_tank">

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

    <link name="base_link">
        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

        <inertial>
            <origin xyz="0.0115 0.000 0.004" rpy="0.000 0.000 0.000"/>
            <mass value="1.02"/>
            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
        </inertial>
    </link>


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

    <link name="imu_link"/>
    <joint name="imu_joint" type="fixed">
        <parent link="base_link"/>
        <child link="imu_link"/>
        <origin xyz="0.000 0.000 0.078" rpy="0.000 0.000 0.000"/>  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
    </joint>




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

    <link name="standoff_l2">
        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
    </link>
    <joint name="standoff_l2_joint" type="fixed">
        <parent link="base_link"/>
        <child link="standoff_l2"/>
        <origin xyz="-0.067 0.044 0.057"/>
    </joint>

    <link name="standoff_l1">
        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
    </link>
    <joint name="standoff_l1_joint" type="fixed">
        <parent link="base_link"/>
        <child link="standoff_l1"/>
        <origin xyz="0.015 0.044 0.057"/>

    </joint>

        <link name="standoff_l3">
        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
    </link>
    <joint name="standoff_l3_joint" type="fixed">
        <parent link="base_link"/>
        <child link="standoff_l3"/>
        <origin xyz="0.071 0.044 0.057"/>
    </joint>


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

    <link name="standoff_r2">
        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
    </link>
    <joint name="standoff_r2_joint" type="fixed">
        <parent link="base_link"/>
        <child link="standoff_r2"/>
        <origin xyz="-0.067 -0.044 0.057"/>
    </joint>

    <link name="standoff_r1">
        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
    </link>
    <joint name="standoff_r1_joint" type="fixed">
        <parent link="base_link"/>
        <child link="standoff_r1"/>
        <origin xyz="0.015 -0.044 0.057"/>

    </joint>

        <link name="standoff_r3">
        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
    </link>
    <joint name="standoff_r3_joint" type="fixed">
        <parent link="base_link"/>
        <child link="standoff_r3"/>
        <origin xyz="0.071 -0.044 0.057"/>
    </joint>



    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
    <link name="platform">
        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
    </link>
    <joint name="platform_joint" type="fixed">
        <parent link="base_link"/>
        <child link="platform"/>
        <origin xyz="0.000 0.000 0.082"/>
    </joint>



    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
    <link name="lidar_standoff_fl">
        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
    </link>
    <joint name="lidar_standoff_fl_joint" type="fixed">
        <parent link="platform"/>
        <child link="lidar_standoff_fl"/>
        <origin xyz="0.072 0.032 0.015"/>
    </joint>

    <link name="lidar_standoff_fr">
        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
    </link>
    <joint name="lidar_standoff_fr_joint" type="fixed">
        <parent link="platform"/>
        <child link="lidar_standoff_fr"/>
        <origin xyz="0.072 -0.032 0.015"/>
    </joint>

    <link name="lidar_standoff_rl">
        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
    </link>
    <joint name="lidar_standoff_rl_joint" type="fixed">
        <parent link="platform"/>
        <child link="lidar_standoff_rl"/>
        <origin xyz="0.015 0.025 0.015"/>
    </joint>

    <link name="lidar_standoff_rr">
        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
    </link>
    <joint name="lidar_standoff_rr_joint" type="fixed">
        <parent link="platform"/>
        <child link="lidar_standoff_rr"/>
        <origin xyz="0.015 -0.025 0.015"/>
    </joint>



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

    <link name="lidar_link">
        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
    </link>
    <joint name="lidar_joint" type="fixed">
        <parent link="platform"/>
        <child link="lidar_link"/>
        <origin xyz="0.050 0.000 0.030" rpy="0.000 0.000 3.1416"/>
    </joint>




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
<link name="left_drive">
    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
    <inertial>
        <mass value="0.05"/>
        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
    </inertial>
</link>
<joint name="left_drive_joint" type="continuous">
    <parent link="base_link"/>
    <child link="left_drive"/>
    <origin xyz="-0.0579 0.068 0.001" rpy="-1.5708 0.000 0.000"/>
    <axis xyz="0 0 1"/>
</joint>


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
<link name="right_drive">
    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
    <inertial>
        <mass value="0.05"/>
        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
    </inertial>
</link>
<joint name="right_drive_joint" type="continuous">
    <parent link="base_link"/>
    <child link="right_drive"/>
    <origin xyz="0.058 -0.068 0.001" rpy="-1.5708 0.000 0.000"/>
    <axis xyz="0 0 1"/>
</joint>



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
<link name="left_bearing">
    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
    <inertial>
        <mass value="0.05"/>
        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
    </inertial>
</link>
<joint name="left_bearing_joint" type="continuous">
    <parent link="base_link"/>
    <child link="left_bearing"/>
    <origin xyz="0.058 0.0686 0.001" rpy="-1.5708 0.000 0.000"/>
    <axis xyz="0 0 1"/>
</joint>

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
<link name="right_bearing">
    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
    <inertial>
        <mass value="0.05"/>
        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
    </inertial>
</link>
<joint name="right_bearing_joint" type="continuous">
    <parent link="base_link"/>
    <child link="right_bearing"/>
    <origin xyz="-0.058 -0.069 0.001" rpy="-1.5708 0.000 0.000"/>
    <axis xyz="0 0 1"/>
</joint>



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
<link name="ultrasonic_left_link">
    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
</link>
<joint name="ultrasonic_left_joint" type="fixed">
    <parent link="base_link"/>
    <child link="ultrasonic_left_link"/>
    <origin xyz="0.01 0.05 0.042" rpy="0.000 0.000 0.000"/>
</joint>


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
<link name="ultrasonic_right_link">
    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
</link>
<joint name="ultrasonic_right_joint" type="fixed">
    <parent link="base_link"/>
    <child link="ultrasonic_right_link"/>
    <origin xyz="0.01 -0.05 0.042" rpy="0.000 0.000 3.1416"/>
</joint>


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
<link name="ultrasonic_back_link">
    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
</link>
<joint name="ultrasonic_back_joint" type="fixed">
    <parent link="base_link"/>
    <child link="ultrasonic_back_link"/>
    <origin xyz="-0.085 0.000 0.012" rpy="0.000 0.000 1.5708"/>
</joint>

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
<link name="ultrasonic_front_link">
    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
</link>
<joint name="ultrasonic_front_joint" type="fixed">
    <parent link="base_link"/>
    <child link="ultrasonic_front_link"/>
    <origin xyz="0.08 0.000 0.042" rpy="0.000 0.000 -1.5708"/>
</joint>








</robot>

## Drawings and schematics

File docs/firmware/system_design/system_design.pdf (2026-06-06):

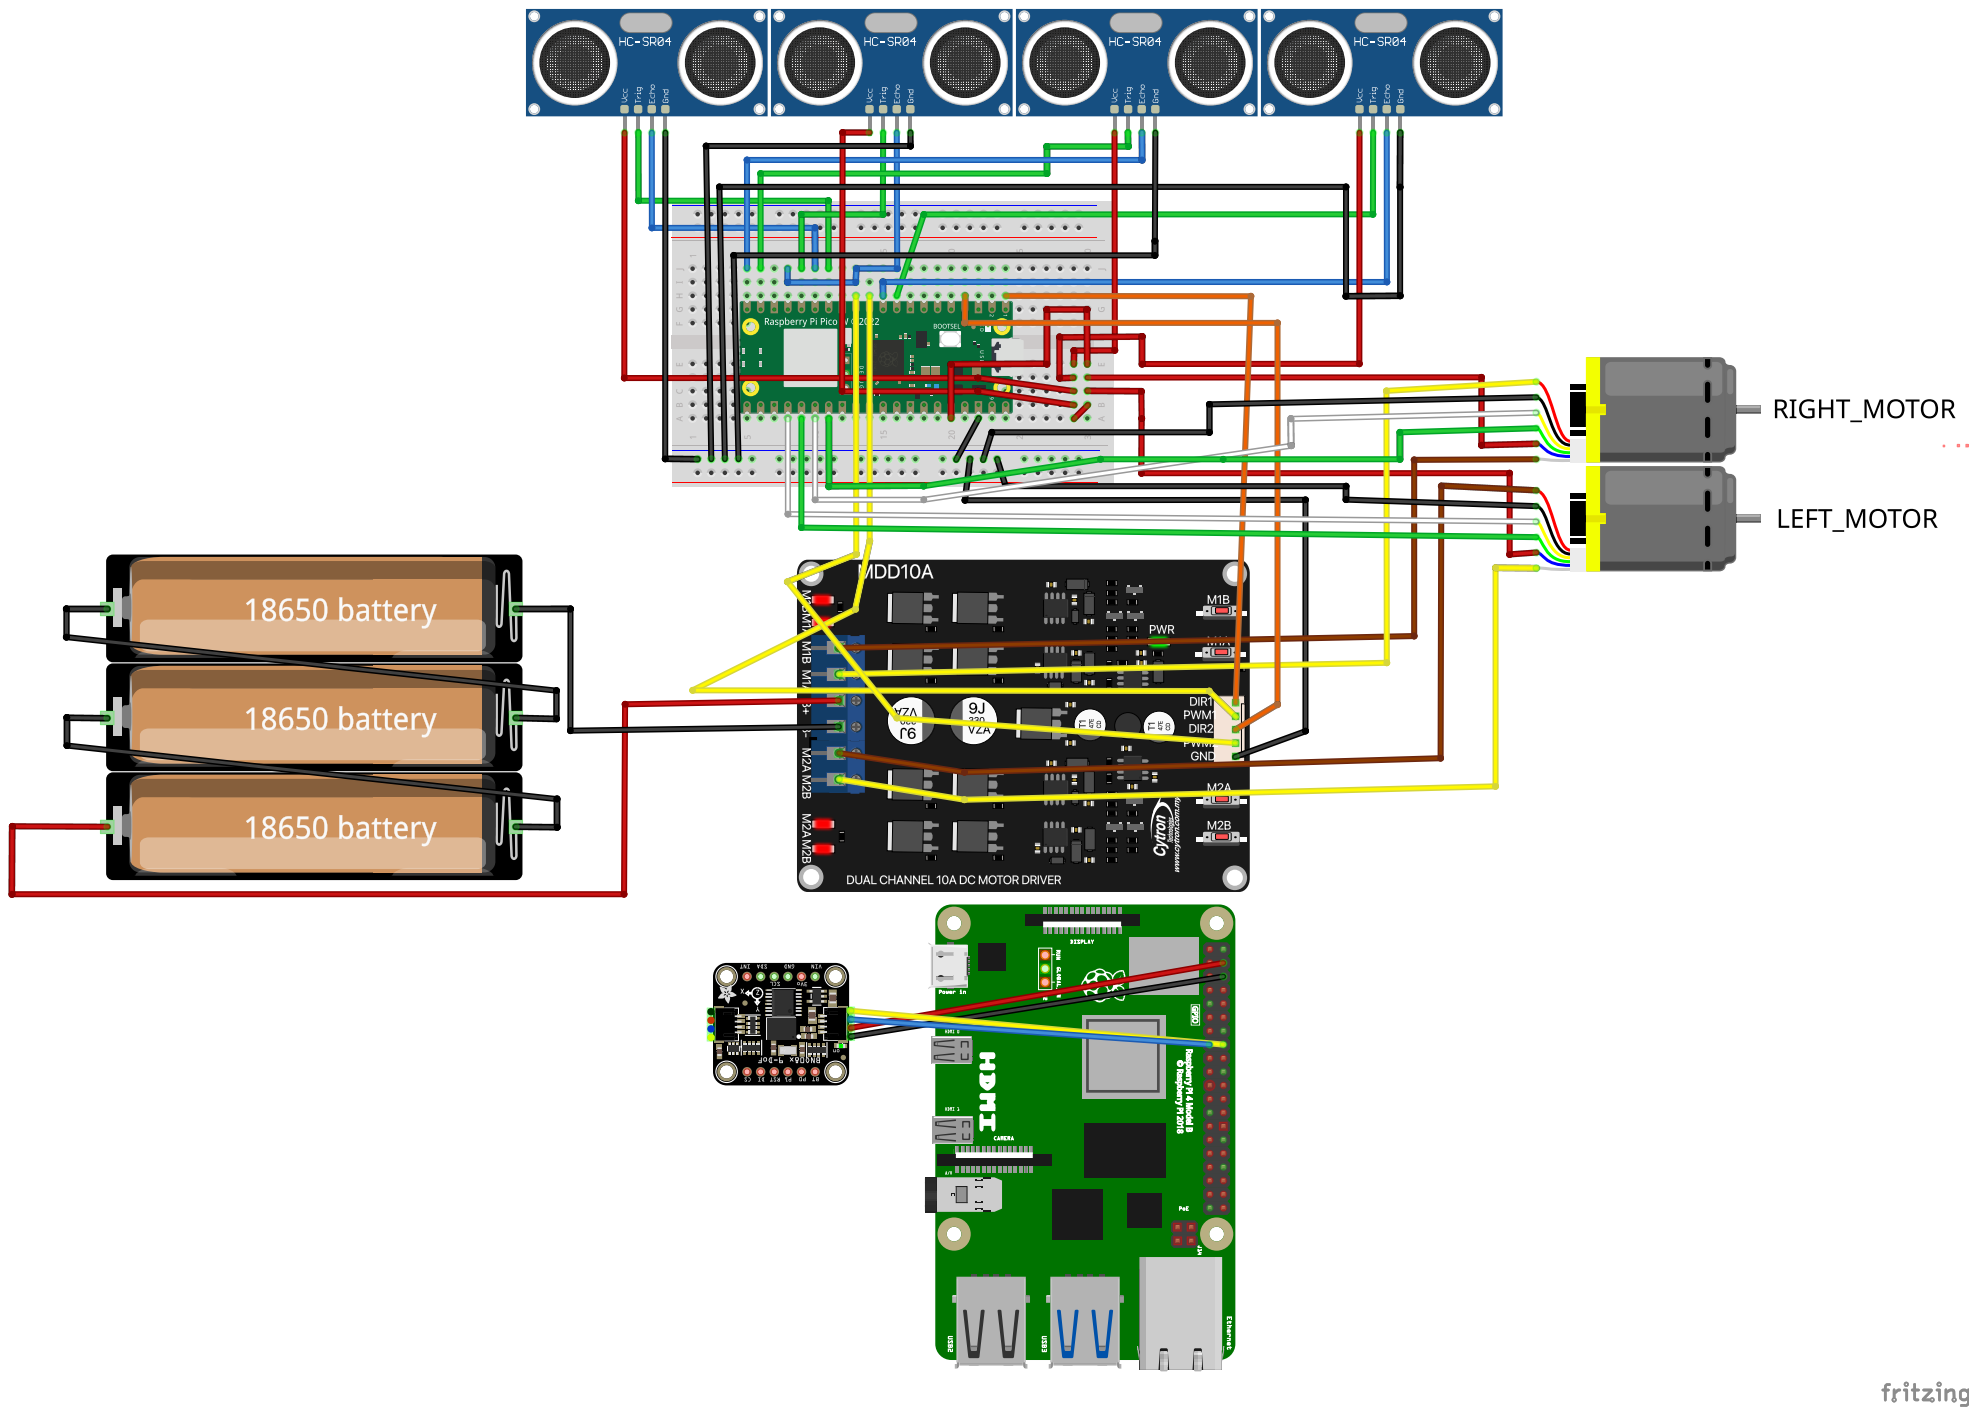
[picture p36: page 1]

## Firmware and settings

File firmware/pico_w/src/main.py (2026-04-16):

from machine import Pin, PWM 
import time 
import machine 

DRIVE_DUTY  = 0.85
TURN_DUTY   = 0.80

class Electronics:
    def __init__(self, name, status):
        self.name = name
        self.status = status

    def ShowStatus(self):
        print(f"{self.name} initialized.")

    def CheckStatus(self):
        print(f"{self.name} disconnected.")


# NOTE: Quadrature Incremental Magnetic Encoder
class Encoder(Electronics):
    _PPR = 11   # Pulses per revolution - the number of possible highs and lows per rev PER PIN !!

    def __init__(self, name, status, _pin_a, _pin_b, _reduction_ratio = 1, _diameter=4.7):
        super().__init__(name, status)
        # Pull up holds the pins at HIGH when no signal is present, this is to prevent floating inputs
        self._pin_a = Pin(_pin_a, Pin.IN, Pin.PULL_UP)
        self._pin_b = Pin(_pin_b, Pin.IN, Pin.PULL_UP)

        self._reduction_ratio = _reduction_ratio
        self._diameter = _diameter # 4.7cm
        self._circumference = 2 * 3.141592653589793 * (_diameter/2)
        self._cpr_motor = 4 * self._PPR     # Counts per revolution OF SHAFT measures the highs and lows on both A and B (QUADRATURE)
        self._cpr_output = self._cpr_motor * self._reduction_ratio # Counts per revolution OF WHEEL measured with the highs and lows of both A and B

        # State variables
        self.count = 0
        self._last_count = 0
        self._last_time = time.ticks_us()

        self._pin_a.irq(trigger=Pin.IRQ_RISING | Pin.IRQ_FALLING, handler=self._callback_a)     # Whenever pin rising or falling, stop all tasks first and run _callback_a function 
        self._pin_b.irq(trigger=Pin.IRQ_RISING | Pin.IRQ_FALLING, handler=self._callback_b)      # Whenever pin rising or falling, stop all tasks first and run _callback_b function 

    def _callback_a(self, _pin_a):         
        a = _pin_a.value()
        b = self._pin_b.value()
        if a == b:
            self.count -= 1         
        else:
            self.count += 1        

    def _callback_b(self, _pin_b):         
        a = self._pin_a.value()
        b = _pin_b.value()
        if a == b:
            self.count += 1         
        else:
            self.count -= 1        

    def get_count(self):
        return self.count
    
    def get_vel(self):
        _now_time = time.ticks_us()
        time_diff = time.ticks_diff(_now_time, self._last_time)
        if time_diff <= 0:
            return 0.0
        
        time_diff = time_diff * 1e-6                                # convert from micro seconds to seconds    
        vel = self._get_distance_delta() / time_diff
        self._last_time = _now_time                                 # reset
        self._last_count = self.count
        return vel                                                  # in cm/s
    
    "Helper Method (Private Method) to calculate distance change since last velocity check."
    def _get_distance_delta(self):
        count_diff = self.count - self._last_count
        distance_diff = (count_diff / self._cpr_output) * self._circumference
        return distance_diff


class Ultrasonic(Electronics):
    def __init__(self, name, status, trigger_pin, echo_pin, current=15e-3, voltage=5, sound_vel=340):
        super().__init__(name, status)
        self.trigger_pin = Pin(trigger_pin, Pin.OUT)
        self.echo_pin = Pin(echo_pin, Pin.IN)
        self.sound_vel = sound_vel          # 340m/s
    
    def distance(self):
        self.trigger_pin.low()              # send 0 to ultrasonic sensor
        time.sleep_us(2)                    # sleep for 2 microseconds
        self.trigger_pin.high()             # send 1 to ultrasonic sensor
        time.sleep_us(10)                   # 10us for input (into sensor) to register
        self.trigger_pin.low()

        timeout = time.ticks_us()
        while not self.echo_pin.value():    # if ECHO is 0 (False) ---> not ECHO is 1 (True)
            if time.ticks_diff(time.ticks_us(), timeout) > 38000:
                return None                     # sensor not responding
            
        time1 = time.ticks_us()             # Start Stopwatch
        while self.echo_pin.value():
            if time.ticks_diff(time.ticks_us(), timeout) > 38000:
                return "out of range"
        time2 = time.ticks_us()             # Stop Stopwatch
        diff = time.ticks_diff(time2, time1)
        if diff > 38000:                    # If out of range
            return "out of range"
        else:
            dist = (diff * 1e-6 * self.sound_vel / 2) * 100
            return dist     # in cm


""" ----------- THIS IS FOR L289N -----------------
class Motor(Electronics):     # TAKES IN (0.2, 0.4) from RPI4
    def __init__(self, name, status, l_in1, l_in2, l_en, r_in1, r_in2, r_en, freq=1907):
        super().__init__(name, status)
        self.l_in1 = Pin(l_in1, Pin.OUT)
        self.l_in2 = Pin(l_in2, Pin.OUT)
        self.l_pwm = PWM(Pin(l_en));  self.l_pwm.freq(freq)

        self.r_in1 = Pin(r_in1, Pin.OUT)
        self.r_in2 = Pin(r_in2, Pin.OUT)
        self.r_pwm = PWM(Pin(r_en));  self.r_pwm.freq(freq)

    def _set(self, in1, in2, pwm, speed):               # private class (speed between -1 to 1)
        speed = max(-1.0, min(1.0, speed))              # used to clamp speed within -1 to 1
        if speed > 0:   in1.value(0); in2.value(1)      # THIS IS FOR DIRECTION (W)
        elif speed < 0: in1.value(1); in2.value(0)      # THIS IS FOR DIRECTION (S)
        else:           in1.value(1); in2.value(1)      # THIS IS FOR DIRECTION (STOP)
        pwm.duty_u16(int(abs(speed) * 65535))           # 0 - 65535 (DUTY CYCLE - CHANGE SPEED)

    def move(self, left, right):
        self._set(self.l_in1, self.l_in2, self.l_pwm, left)
        self._set(self.r_in1, self.r_in2, self.r_pwm, right)

    # THIS IS FOR FIXED MOVEMENTS
    def forward(self):          self.move( DRIVE_DUTY,  DRIVE_DUTY)
    def backward(self):         self.move(-DRIVE_DUTY, -DRIVE_DUTY)
    def tank_turn_left(self):   self.move( TURN_DUTY, -TURN_DUTY)
    def tank_turn_right(self):  self.move(-TURN_DUTY,  TURN_DUTY)
    def stop(self):             self.move(0, 0)
"""


"This is for Cytron MDD10A ---> which only requires direction pin and pwm pin per motor"
class Motor(Electronics):     
    def __init__(self, name, status, l_dir, l_pwm, r_dir, r_pwm, freq=1907):
        super().__init__(name, status)
        self.l_dir = Pin(l_dir, Pin.OUT)
        self.l_pwm = PWM(Pin(l_pwm))
        self.l_pwm.freq(freq)

        self.r_dir = Pin(r_dir, Pin.OUT)
        self.r_pwm = PWM(Pin(r_pwm))
        self.r_pwm.freq(freq)

    def _set(self, dir_pin, pwm_pin, speed):            
        speed = max(-1.0, min(1.0, speed))              # Clamp speed within -1 to 1
        
        if speed > 0:   
            dir_pin.value(1)                            # Set direction (Forward)
        elif speed < 0: 
            dir_pin.value(0)                            # Set direction (Reverse)
        else:           
            dir_pin.value(0)                            # Direction doesn't matter if speed is 0
            
        pwm_pin.duty_u16(int(abs(speed) * 65535))       # 0 - 65535 (DUTY CYCLE)

    # Simply combines both left and right together for teleop control
    def move(self, left, right):
        self._set(self.l_dir, self.l_pwm, left)
        self._set(self.r_dir, self.r_pwm, right)

    # THIS IS FOR FIXED MOVEMENTS
    def forward(self):          self.move( DRIVE_DUTY,  DRIVE_DUTY)
    def backward(self):         self.move(-DRIVE_DUTY, -DRIVE_DUTY)
    def tank_turn_left(self):   self.move( TURN_DUTY, -TURN_DUTY)
    def tank_turn_right(self):  self.move(-TURN_DUTY,  TURN_DUTY)
    def stop(self):             self.move(0, 0)

class PID:
    def __init__(self, kp, ki, kd, setpoint=0.0):
        self.kp = kp
        self.ki = ki
        self.kd = kd
        self.setpoint = setpoint

        self.integral = 0.0
        self.previous_error = 0.0
        self.last_time = time.ticks_us()

    def calculate(self, setpoint, current_value):
        current_time = time.ticks_us()
        dt = time.ticks_diff(current_time, self.last_time) / 1000000 # Convert ms to seconds

        if dt <= 0.0:
            dt = 0.01
        
        error = setpoint - current_value
        self.integral += error * dt
        self.integral = max(-10.0, min(10.0, self.integral))
        
        p_term = self.kp * error
        i_term = self.ki * self.integral
        d_term = self.kd * ((error - self.previous_error) / dt) 
        
        self.previous_error = error
        self.last_time = current_time

        output = p_term + i_term + d_term
        return output


# INITIALIZING COMPONENTS
USRM_TL = Ultrasonic("TL", "ON", trigger_pin=6, echo_pin=7)
USRM_TR = Ultrasonic("TR", "ON", trigger_pin=10, echo_pin=11) 
USRM_BL = Ultrasonic("BL", "ON", trigger_pin=12, echo_pin=13)
USRM_BR = Ultrasonic("BR", "ON", trigger_pin=14, echo_pin=15)
MOTOR = Motor("LEFT_RIGHT_MOTORS","ON", l_dir=0, l_pwm=8, r_dir=2, r_pwm=9)
LEFT_ENCODER = Encoder("L_ENC", "ON", _pin_a=16, _pin_b=17)
RIGHT_ENCODER = Encoder("R_ENC", "ON", _pin_a=18, _pin_b=19)
PID = PID(999, 999, 999)
USRM_TL.ShowStatus()
USRM_TR.ShowStatus()
USRM_BL.ShowStatus()
USRM_BR.ShowStatus()
MOTOR.ShowStatus()
LEFT_ENCODER.ShowStatus()
RIGHT_ENCODER.ShowStatus()

# MAIN LOOP
while True:
    data = input().strip()         # receives "(0.85, 0.75)" ---> "(left_motor_pwm, right_motor_pwm)"
    try:
        left, right = map(float, data.strip("()").split(","))
        MOTOR.move(left, right)
        print(f"Changed pwm for motors to {left} and {right} respectively")
    except:
        print("ERROR: Change of speed.")

    dist = []
    dist.append(USRM_TL.distance())
    dist.append(USRM_TR.distance())
    dist.append(USRM_BL.distance())
    dist.append(USRM_BR.distance())

    for element in dist:
        if isinstance(element, (int, float)):
            if element < 3:
                MOTOR.stop()
                break
    
    
        
    

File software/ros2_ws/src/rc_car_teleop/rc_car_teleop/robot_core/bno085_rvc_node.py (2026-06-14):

#!/usr/bin/env python3
"""BNO085 IMU node over UART in RVC mode.

Reads yaw, pitch, roll, and linear acceleration from a BNO085 IMU in UART RVC
mode and publishes them as ``sensor_msgs/msg/Imu`` on ``/sensors/imu``. RVC
mode does not provide angular velocity, so that field is left at zero and its
covariance is set to negative one to mark it as unknown.
"""

import math
import os
import subprocess
import time

import serial
from adafruit_bno08x_rvc import BNO08x_RVC

import rclpy
from rclpy.node import Node
from sensor_msgs.msg import Imu


def free_serial_port(port: str) -> None:
    """Free the serial port by killing any process still holding it.

    Args:
        port (str): the serial port path, such as ``/dev/serial0``.
    """
    try:
        real = os.path.realpath(port)
        subprocess.run(['fuser', '-k', real],
                       stdout=subprocess.DEVNULL,
                       stderr=subprocess.DEVNULL,
                       check=False)
        time.sleep(0.5)
    except FileNotFoundError:
        pass


def euler_to_quaternion(yaw_deg: float, pitch_deg: float, roll_deg: float):
    """Convert Euler angles in degrees to a quaternion (x, y, z, w).

    Uses the ZYX convention (yaw about Z, pitch about Y, roll about X), which
    matches ROS REP 103.

    Args:
        yaw_deg (float): yaw in degrees.
        pitch_deg (float): pitch in degrees.
        roll_deg (float): roll in degrees.

    Returns:
        tuple: the quaternion as (x, y, z, w).
    """
    yaw   = math.radians(yaw_deg)
    pitch = math.radians(pitch_deg)
    roll  = math.radians(roll_deg)

    cy = math.cos(yaw   * 0.5)
    sy = math.sin(yaw   * 0.5)
    cp = math.cos(pitch * 0.5)
    sp = math.sin(pitch * 0.5)
    cr = math.cos(roll  * 0.5)
    sr = math.sin(roll  * 0.5)

    w = cr * cp * cy + sr * sp * sy
    x = sr * cp * cy - cr * sp * sy
    y = cr * sp * cy + sr * cp * sy
    z = cr * cp * sy - sr * sp * cy

    return x, y, z, w


class BNO085RVCNode(Node):
    """ROS 2 node that publishes BNO085 IMU data read over UART in RVC mode.

    Publishes:
        ``/sensors/imu`` (sensor_msgs/msg/Imu): orientation and linear
        acceleration.

    Parameters:
        serial_port (str): serial device path. Default ``/dev/serial0``.
        baudrate (int): serial baud rate. Default 115200.
        frame_id (str): frame id for the IMU messages. Default ``imu_link``.
        publish_rate (double): publish rate in Hz. Default 50.
    """

    def __init__(self):
        """Free the serial port, open it, and start the publish timer."""
        super().__init__('bno085_rvc')

        self.declare_parameter('serial_port', '/dev/serial0')
        self.declare_parameter('baudrate', 115200)
        self.declare_parameter('frame_id', 'imu_link')
        self.declare_parameter('publish_rate', 50.0)

        port     = self.get_parameter('serial_port').value
        baudrate = self.get_parameter('baudrate').value
        self.frame_id = self.get_parameter('frame_id').value
        rate     = self.get_parameter('publish_rate').value

        self.get_logger().info(f'Clearing any stale holders of {port}...')
        free_serial_port(port)

        self.get_logger().info(f'Opening {port} at {baudrate} baud...')
        self.uart = None
        for attempt in range(5):
            try:
                self.uart = serial.Serial(port, baudrate=baudrate, timeout=1.0)
                break
            except serial.SerialException as e:
                self.get_logger().warn(
                    f'Open failed (attempt {attempt + 1}/5): {e}'
                )
                time.sleep(1.0)
        if self.uart is None:
            raise RuntimeError(f'Could not open {port} after 5 attempts')

        time.sleep(1.0)
        self.uart.reset_input_buffer()
        self.rvc = BNO08x_RVC(self.uart)
        self.get_logger().info('BNO085 RVC connected.')

        self.imu_pub = self.create_publisher(Imu, '/sensors/imu', 10)

        self._consec_errors = 0

        period = 1.0 / rate
        self.timer = self.create_timer(period, self.timer_callback)

        self.get_logger().info(
            f'Publishing sensor_msgs/Imu on /sensors/imu at {rate} Hz'
        )

    def timer_callback(self):
        """Read one RVC sample, convert it, and publish it as an Imu message."""
        try:
            yaw, pitch, roll, x_accel, y_accel, z_accel = self.rvc.heading
            self._consec_errors = 0
        except Exception:
            self._consec_errors += 1
            if self._consec_errors >= 25:
                try:
                    self.uart.reset_input_buffer()
                except Exception:
                    pass
                self._consec_errors = 0
                self.get_logger().warn('Stream out of sync, flushed buffer.')
            return

        qx, qy, qz, qw = euler_to_quaternion(yaw, pitch, roll)

        msg = Imu()

        msg.header.stamp    = self.get_clock().now().to_msg()
        msg.header.frame_id = self.frame_id

        msg.orientation.x = qx
        msg.orientation.y = qy
        msg.orientation.z = qz
        msg.orientation.w = qw
        msg.orientation_covariance[0] = 0.01
        msg.orientation_covariance[4] = 0.01
        msg.orientation_covariance[8] = 0.01

        msg.angular_velocity.x = 0.0
        msg.angular_velocity.y = 0.0
        msg.angular_velocity.z = 0.0
        msg.angular_velocity_covariance[0] = -1.0

        msg.linear_acceleration.x = float(x_accel)
        msg.linear_acceleration.y = float(y_accel)
        msg.linear_acceleration.z = float(z_accel)
        msg.linear_acceleration_covariance[0] = 0.1
        msg.linear_acceleration_covariance[4] = 0.1
        msg.linear_acceleration_covariance[8] = 0.1

        self.imu_pub.publish(msg)

    def destroy_node(self):
        """Close the serial port and destroy the node."""
        try:
            self.uart.close()
        except Exception:
            pass
        super().destroy_node()


def main(args=None):
    """Start the BNO085 RVC node and spin until interrupted."""
    rclpy.init(args=args)
    node = BNO085RVCNode()
    try:
        rclpy.spin(node)
    except KeyboardInterrupt:
        pass
    finally:
        node.destroy_node()
        try:
            rclpy.shutdown()
        except Exception:
            pass


if __name__ == '__main__':
    main()

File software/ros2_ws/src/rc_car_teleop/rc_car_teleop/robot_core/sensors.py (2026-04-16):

class Electronics:
    def __init__(self, name, status):
        self.name = name
        self.status = status

    def ShowStatus(self):
        print(f"{self.name} initialized.")

    def CheckStatus(self):
        print(f"{self.name} disconnected.")


class Camera(Electronics):
    def __init__(self, name, status, current=55e-3, voltage=1.8, height=720, width=1280, array_size=921600, fps=30, output_format="10-bit_RAW_RGB"):
        super().__init__(name, status, current, voltage)
        self.current = current              # 0.055A
        self.voltage = voltage              # 1.8V
        self.height = height                # 720 pixels
        self.width = width                  # 1080 pixels
        self.array_size = array_size        # 720*1080 = 921600 pixels
        self.fps = fps                      # 60 fps
        self.output_format = output_format  # 10-bit RAW RGB ---> (1280, 720, 3)
    
    # def GetFrames(self, array_size):

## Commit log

2026-04-11 added doc for ultrasonic sensor
2026-04-11 stopped at PID for blueprint
2026-04-12 added PID
2026-04-15 done encoder
2026-04-16 change file name fropm pico motor control to pico w
2026-04-16 changed motor class
2026-04-16 added system design for wiring
    [system_design.fzz]
2026-04-19 fixed main.cpp with ultrasonic publisher
2026-04-20 completed camera.py
    [system_design.fzz]
2026-04-21 - created ROS_architecture - renamed topics across teleop, camera, and main.cpp - rm model.pt, planning to change to YOLO
2026-04-21 - declared fps as parameter in camera - added yolo.py
2026-04-22 renamed topics yolo and camera
2026-04-28 insane progress chat
    [YDLIDAR_X3Pro.stl, full_chassis.stl, tank.urdf]
2026-04-28 fixed package.xml with corrected upper plate dim
    [tank.urdf]
2026-05-01 fixed PID
2026-05-01 comment PID first
2026-05-01 testing for fixed distance, to see left right encoder ticks
2026-05-02 main.cpp fixed encoder ticks
2026-05-03 fixed ultrasonic sensors
2026-05-09 update to reflections (until PID portion)
2026-05-10 fixing PID
2026-05-10 undo fixing PID
2026-05-10 teleop, main, config is final and working: include PID, everything in m/s
2026-05-18 added imu
2026-05-18 fixed imu
2026-05-19 new urdf
    [new_chassis.stl, tank.urdf]
2026-05-20 new debug directory for compiling of debugging firmware for flashing on pico, also changed imu in main to use core 1 for data collection and core 0 for main loop to be run at 100Hz
2026-05-20 no slew rate and pid
2026-05-21 changed variable name in pid (no change to logic)
    updated correct naming for package
2026-05-23 added joint_state_publisher
2026-05-29 add bno085_rvc_node for BNO085 sensor integration and IMU data publishing
2026-05-30 Add URDF and SDF files for tank model and simulation environment
    - Created tank_gazebo.urdf to define the tank model including links, joints, and sensors (LIDAR, IMU).
    - Added tank_world.sdf to set up the simulation environment with physics, lighting, and obstacles for the tank to navigate.
    - Configured Gazebo plugins for differential drive and sensor functionalities.
    [tank_gazebo.urdf, tank_world.sdf]
2026-05-30 Add video and documentation updates for LIDAR setup and BNO085 debugging
2026-05-31 Update odometry calculations: adjust wheel circumference and wheel base values for improved accuracy
2026-05-31 Update ydlidar configuration: adjust baudrate, device type, sample rate, and single channel settings for improved performance
2026-05-31 Add slam.launch.py for SLAM functionality and update tank.urdf mesh filename
    [tank.urdf]
2026-05-31 Adjust odometry update frequency and modify SLAM configuration parameters for improved performance
2026-05-31 Update wheel base parameter for odometry calculations
2026-05-31 Add scan matching parameters and update odometry node in SLAM configuration
2026-06-01 Update BNO085 node to I2C mode and enhance command documentation
2026-06-01 Update commands documentation and enhance EKF configuration for improved odometry and IMU handling
2026-06-01 Refactor BNO085 I2C node to include yaw zeroing and quaternion handling; update EKF configuration to disable differential yaw
2026-06-01 Fix LIDAR standoff positions and adjust base link orientation for correct alignment
    [tank.urdf]
2026-06-01 Update base link orientation in URDF for correct alignment
    [tank.urdf]
2026-06-01 Fix odometry distance calculations and update URDF for correct base link and LIDAR orientations
    [tank.urdf]
2026-06-01 Fix odometry calculations and update EKF configuration for improved yaw handling
    [odom.py]
2026-06-01 Fix base link orientation in URDF for correct alignment
    [tank.urdf]
2026-06-01 Fix IMU and LIDAR orientations in URDF for correct alignment
    [tank.urdf]
2026-06-01 Refine URDF link origins and orientations for improved accuracy
    [tank.urdf]
2026-06-01 Update odom0_config and odom0_twist_covariance_override for improved rotational velocity handling
2026-06-01 Add odom_topic parameter to slam_toolbox configuration for filtered odometry
2026-06-02 Add sensor testing commands and enable diagnostics in EKF configuration
2026-06-02 Increase HOLD_TIMEOUT_MS to 525ms for improved key repeat handling and update EKF configuration to trust forward velocity and yaw orientation.
2026-06-03 Update EKF and SLAM Toolbox configurations for improved velocity handling and mapping performance
2026-06-06 Refactor debug setup and update configurations for motor control and odometry calculations
    [system_design.fzz]
2026-06-10 Update maximum wheel speed and adjust motor inversion settings for improved control
2026-06-10 Update EKF configuration to ignore rotational velocity from odometry and IMU
2026-06-10 Update odometry logging, adjust SLAM toolbox parameters for performance improvements
2026-06-11 Update SLAM toolbox configuration and adjust LIDAR orientation for improved accuracy
    [tank.urdf]
2026-06-11 Fix robot footprint format in costmap configuration for consistency
2026-06-12 Update nav2_params.yaml with explicit paths for behavior trees and fix plugin paths in tank.urdf for consistency
    [tank.urdf]
2026-06-12 Normalize origin values in tank.urdf for consistency and clarity
    [tank.urdf]
2026-06-12 Update imu0_differential setting in ekf.yaml to use absolute yaw for accurate orientation handling
2026-06-12 Refine odometry handling and update EKF and SLAM configurations for improved accuracy and performance
    [tank.urdf]
2026-06-12 Fix LIDAR orientation in tank.urdf for accurate positioning
    [tank.urdf]
2026-06-12 Update controller parameters to improve motor responsiveness and performance
2026-06-12 Add goal pose relay node to zero timestamps and fix TF extrapolation issue
2026-06-12 Update desired linear velocity for the path following controller to improve teleoperation speed control
2026-06-12 Update IMU configuration to use absolute yaw for improved orientation accuracy
2026-06-12 Update controller parameters to enhance velocity thresholds and goal tolerances for improved navigation performance
2026-06-12 Update controller parameters to increase rotate to heading angular velocity and minimum angle for improved navigation responsiveness
2026-06-12 Update navigation launch configuration to include velocity smoother and adjust remappings for improved command velocity handling
2026-06-12 Reorder pin assignments for left and right encoders and motors for consistency
2026-06-12 Invert encoder direction for left and right motors to correct navigation behavior
2026-06-14 Clean up codebase and docs for portfolio
    [tank_gazebo.urdf, tank_world.sdf]
